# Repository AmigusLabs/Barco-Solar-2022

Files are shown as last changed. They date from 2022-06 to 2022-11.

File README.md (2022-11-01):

# Barco-Solar-2022

Hemos creado de nuevo (<a href="https://www.amiguslabs.org/portfolio_page/barco-solar/" target="_blank">Barco 2018</a> -  <a href="https://www.amiguslabs.org/portfolio_page/amigus-labs-barco-solar19/" target="_blank">Barco 2019</a>) un barco impreso en 3d para participar en la <a href="http://regatasolar.org" target="_blank">Regata Solar de Marine Instruments</a>. Esta vez un trimaran de unos 9Kg de peso y un volumen total de 29 litros.

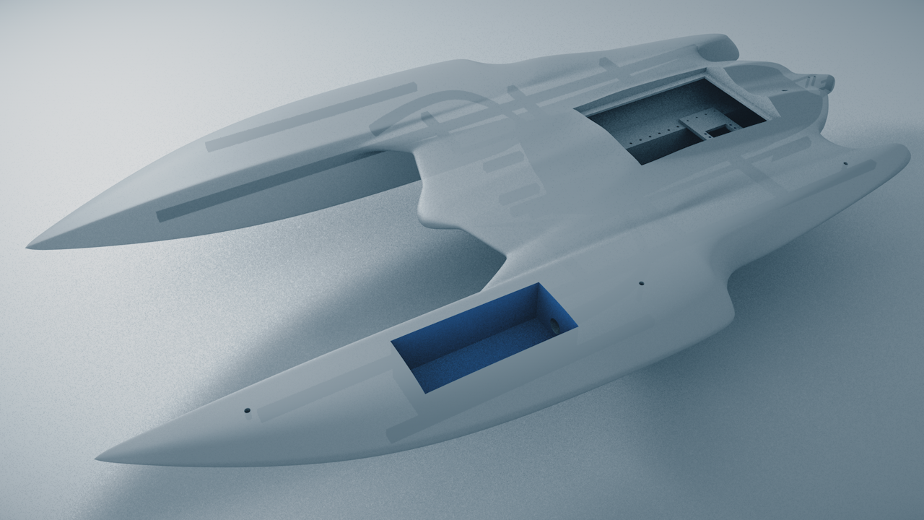
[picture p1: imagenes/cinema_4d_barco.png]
Barco_3D


Se ha diseñado integramente en Cinema 4D, con subdivisión de superficies (curvas Nurbs).

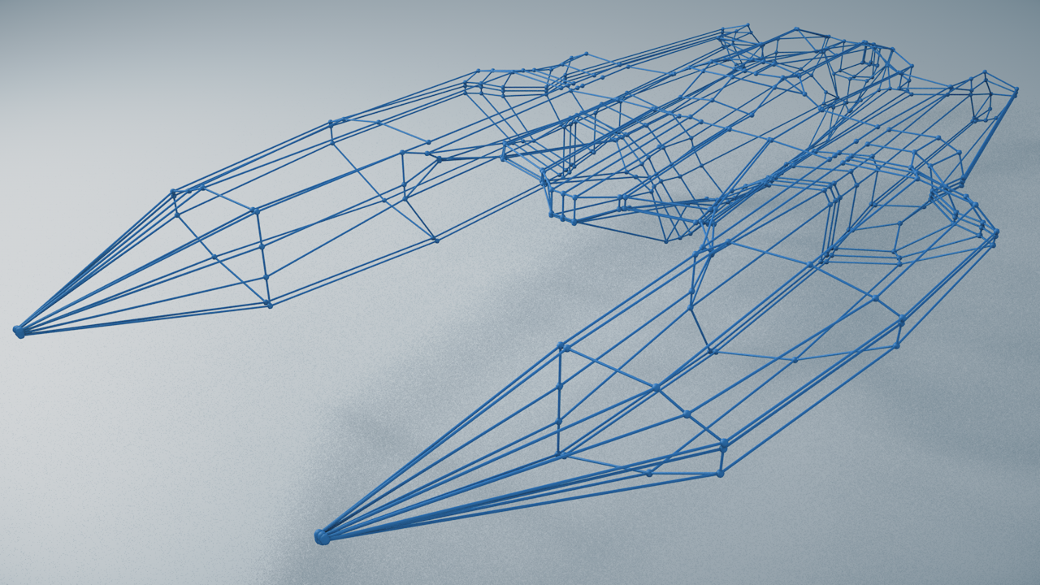
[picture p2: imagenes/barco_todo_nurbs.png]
Nurbs


Una vez modelado, se han dividio en 32 piezas para imprimir, secciones de hasta 250x250x200mm y exportado a STL. Para optimizar la impresión intentamos que cada sección no tardase más de 10 horas en imprimirse, para intentar imprimir por el dia y dormir por la noche :P El software de slicer usado es el Simplify3D y la impresora una Ender 5 Plus.

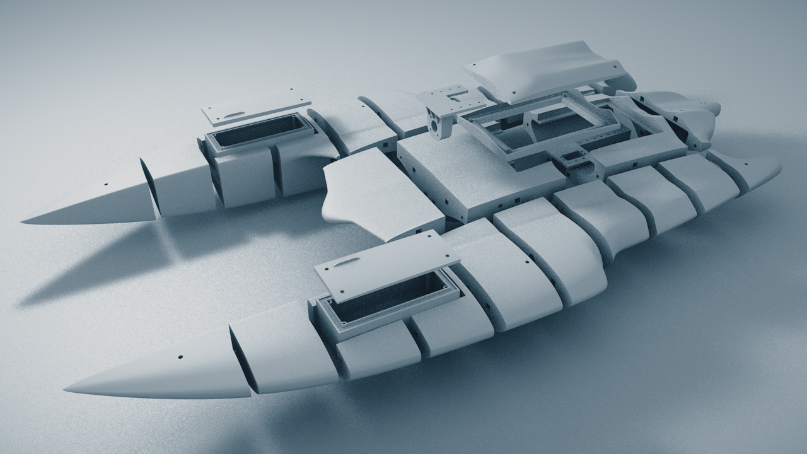
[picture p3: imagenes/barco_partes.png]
Barco_secciones 3D


Evitanto el uso de soportes a la hora de imprimir se han hecho algunas secciones que finalmente se pegan para poder imprimir sobre el lado más plano y evitar luego el postprocesado.

Una vez impresas las piezas, y para facilitar la rigidez a la hora de pegarlas, se han hecho unas secciones en cada pieza para pegar y encajar unos pequeños tubos impresos de unos 10x10x50mm. Se ha pegado todas las partes con pegamento para modelismo comprado en bazar chino, tarda unas 4 horas en secar y quedan las piezas muy rígidas. En las zonas que por sharping de las piezas hizo falta se relleno de masilla para carrocerías de Ceys. 

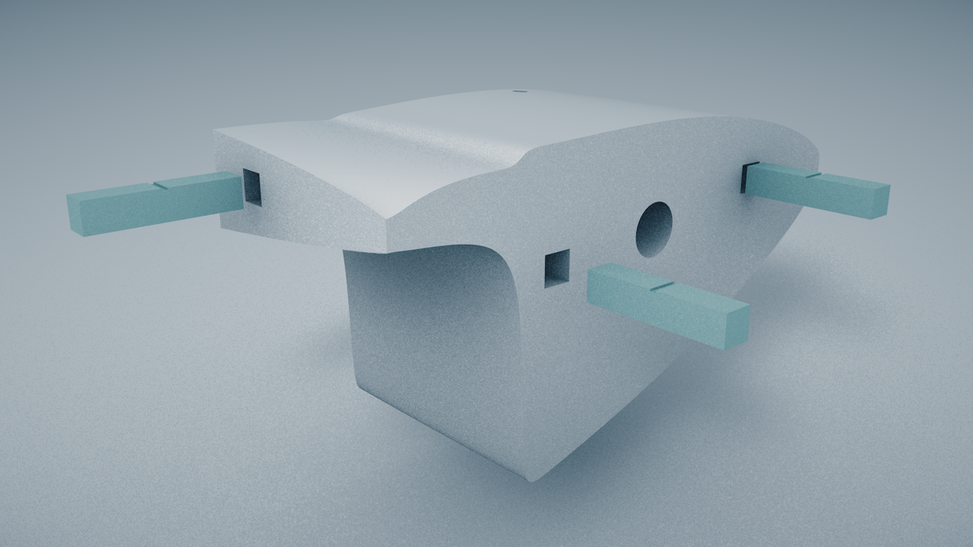
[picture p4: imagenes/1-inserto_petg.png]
Insertos-PETG


Para darle el acabado final, una vez pegadas todas las piezas, se ha aplicado imprimación de color blanco y posteriormente una mano de Epoxi. En el montaje, en las zonas más irregulares se le aplicó un poco de lijado.

Para encajar las partes de electrónica al barco, así como el soporte de la placa solar, se han usado unos insertos de M5 y M3 aplicados con solador, que evitan el uso de tuercas y hacen que las zonas de enrosque queden bien sujetas.

Para las tapas se ha usado goma Eva cortado en laser para hacer las zonas de unión impermeables (gracias a <a href="https://fablableon.org" target="_blank">Fab Lab León</a> y <a href="https://www.esne.es" target="_blank">ESNE</a> por facilitarnos el corte en sus máquinas).

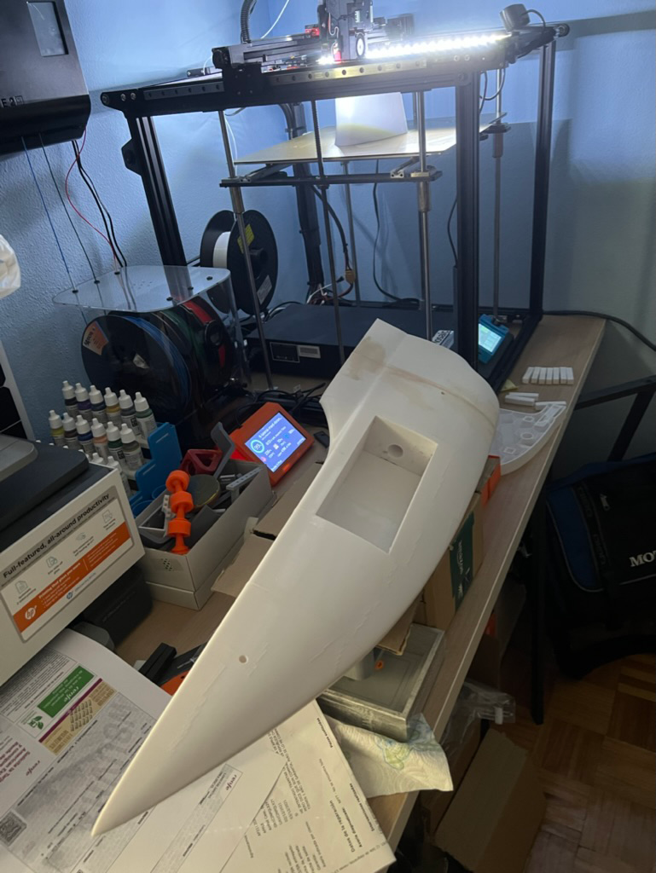
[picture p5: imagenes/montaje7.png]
Montaje


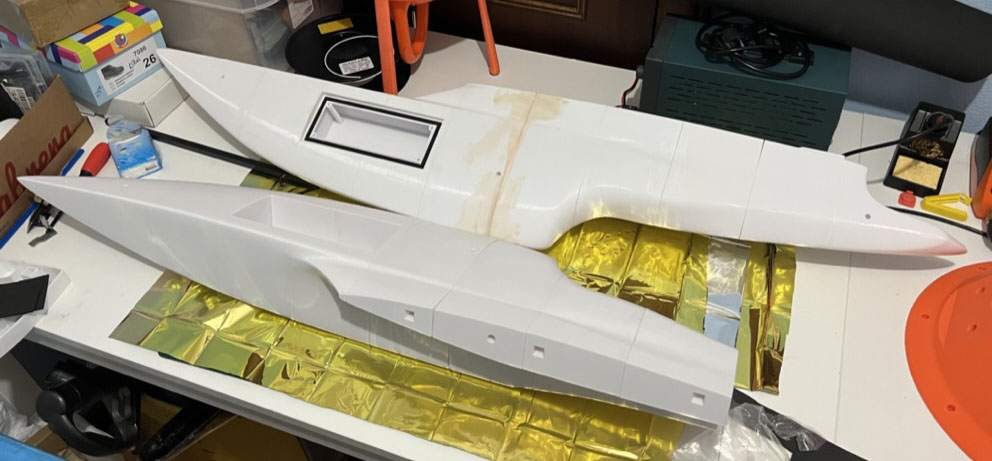
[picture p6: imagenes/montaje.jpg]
Montaje


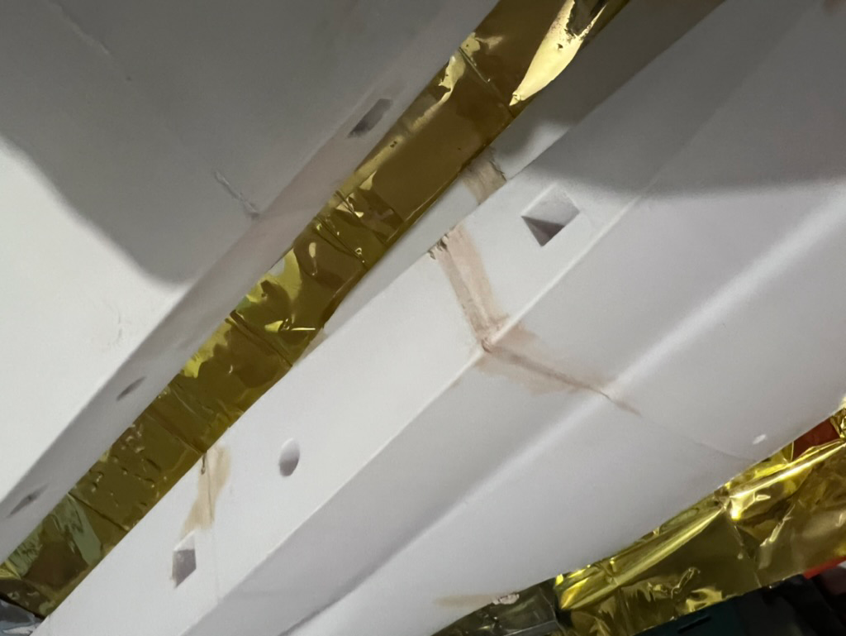
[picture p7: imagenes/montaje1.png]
Montaje


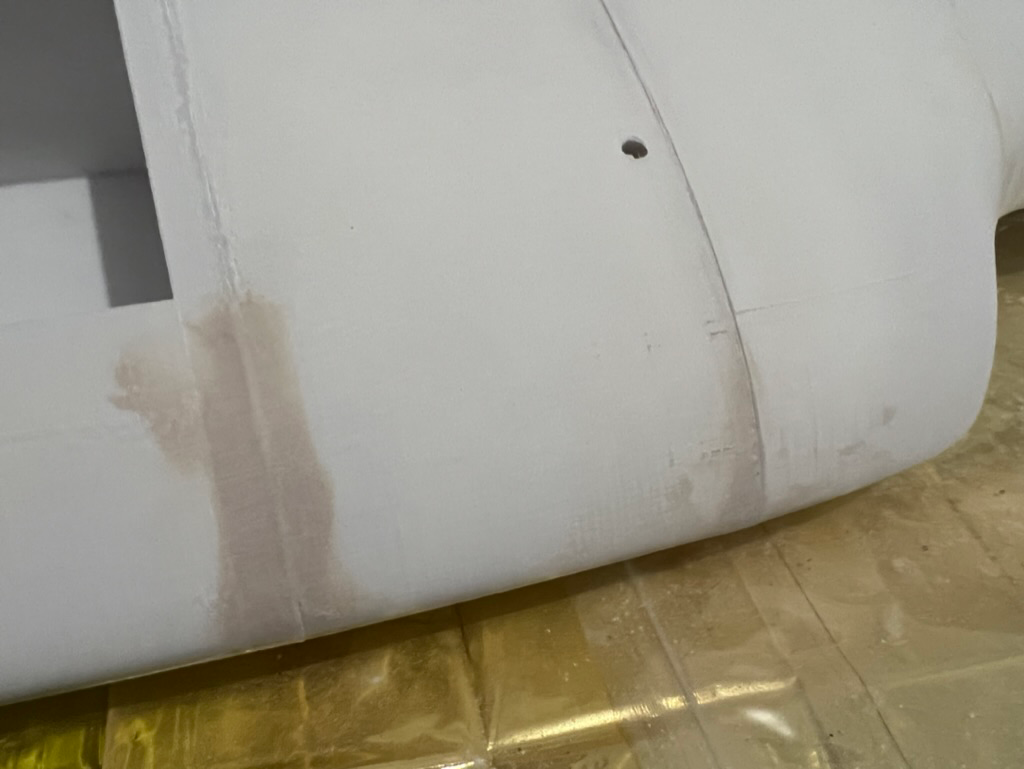
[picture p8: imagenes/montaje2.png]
Montaje


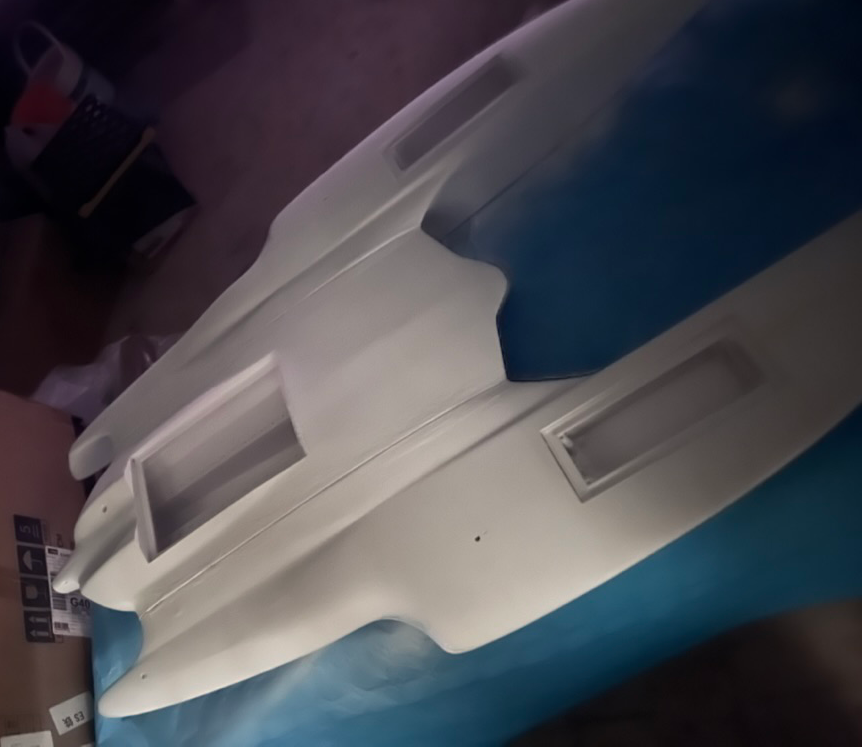
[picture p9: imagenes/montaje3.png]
Montaje


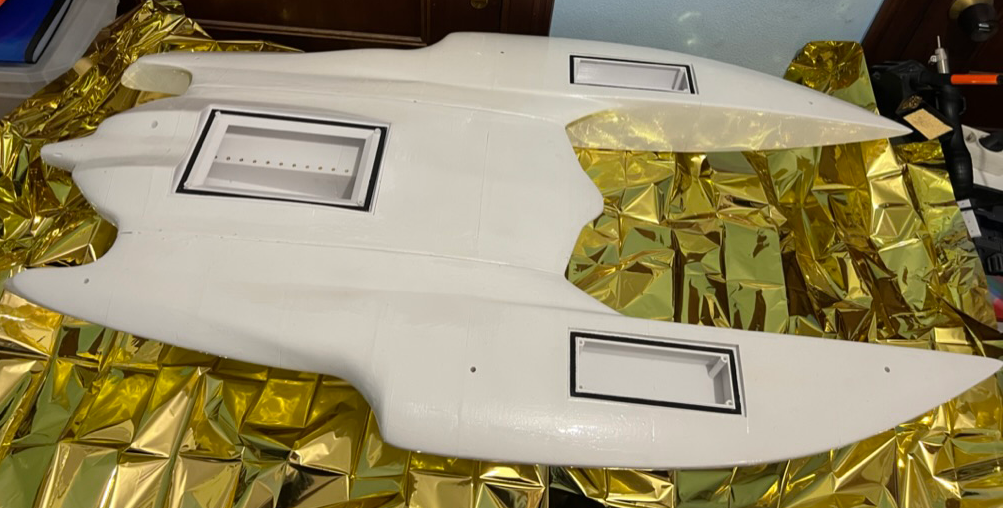
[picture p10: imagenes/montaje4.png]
Montaje


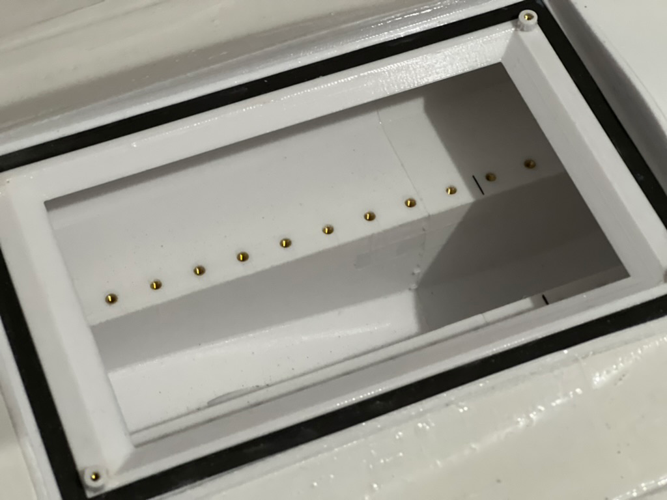
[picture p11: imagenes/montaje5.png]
Montaje


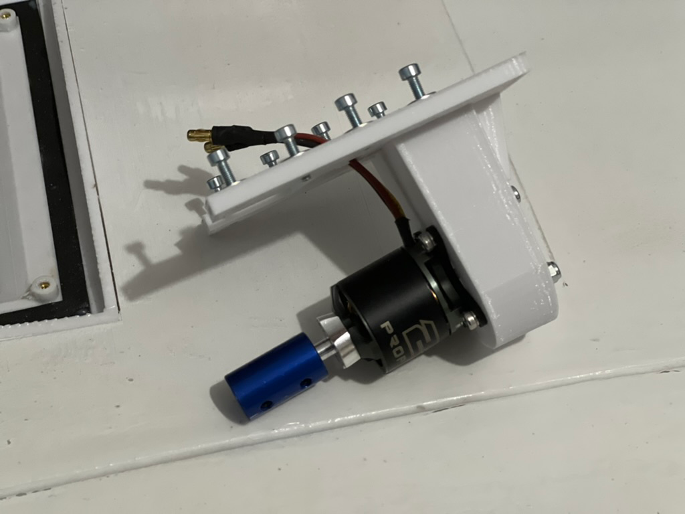
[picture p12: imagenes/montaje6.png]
Montaje


## Electrónica

Hemos intentado hacer una nueva PCB partiendo de un Attiny1614. Se ha diseñado la pcb en KiCAD, integrando un sensor INA219 para la optimización del voltaje y potencia de la placa solar basandonos en la propuesta de <a href="https://github.com/aindustriosa/Solar_MPPT_board" target="_blank">A Industriosa</a> del año 2019.

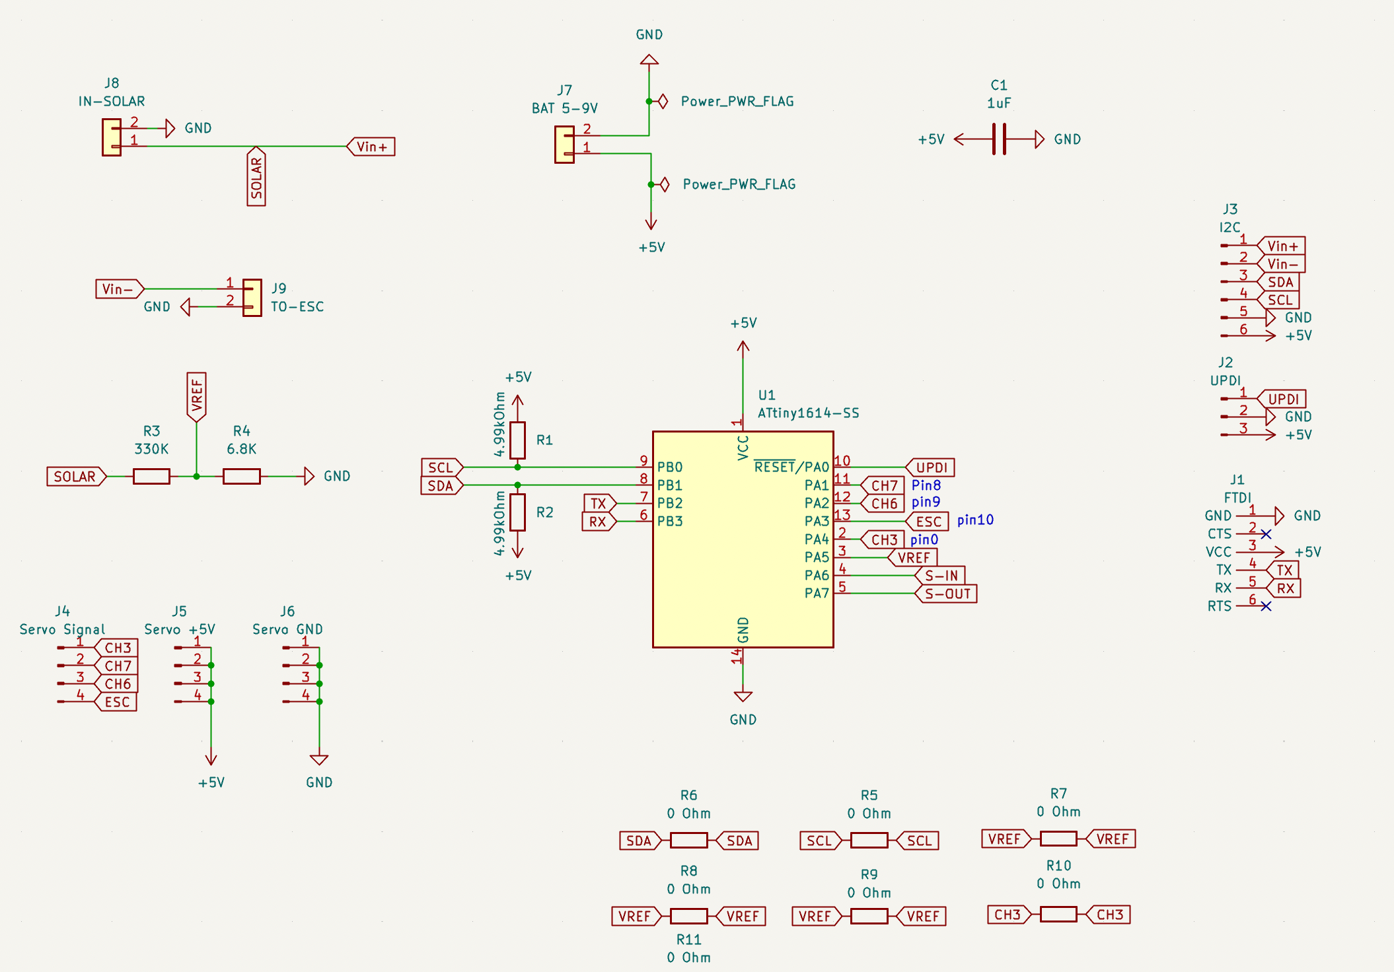
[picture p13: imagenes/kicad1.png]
KiCAD


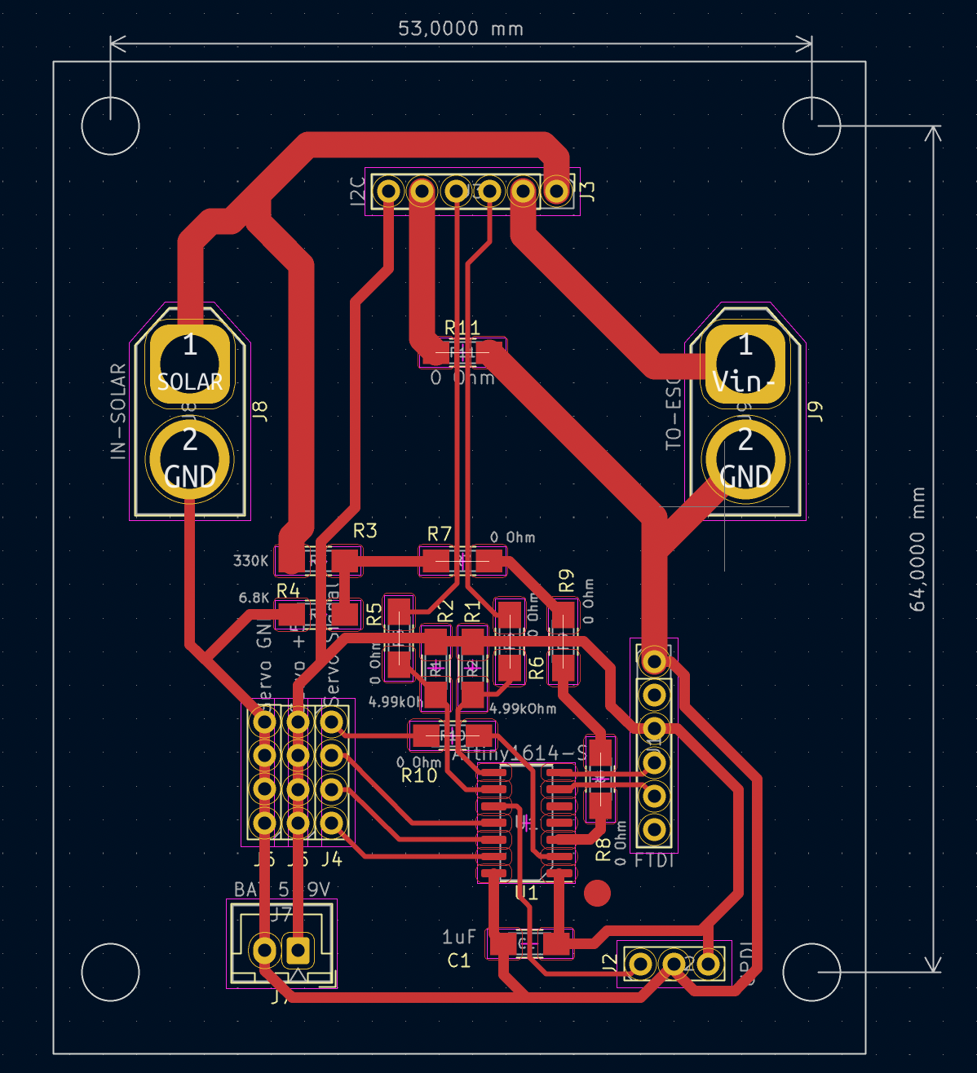
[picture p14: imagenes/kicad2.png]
KiCAD


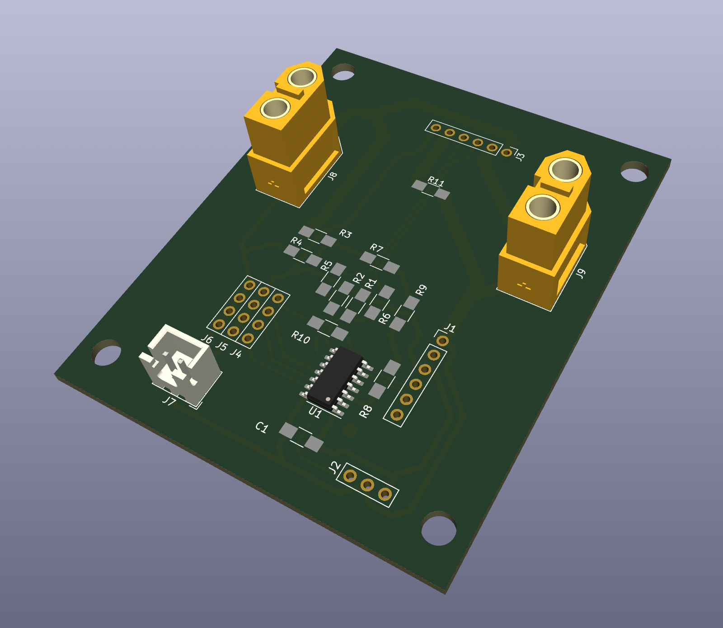
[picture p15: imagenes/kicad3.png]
KiCAD


Con los limites de potencia y memoria del Attiny1614, hemos implementado el uso del sensor así como un divisor de voltaje para leerlo via VREF. Los mensajes enviados desd eel mando RC al receptor, son procesados por el microcontrolador y en caso de exigirle una velocidad mayor al 30% entra en modo automático, y prioriza el rendimiento que este generando la placa solar en ese momento a optener la velocidad optima sin permitir la caida de potencia por un exceso del rendimiento de la placa solar.

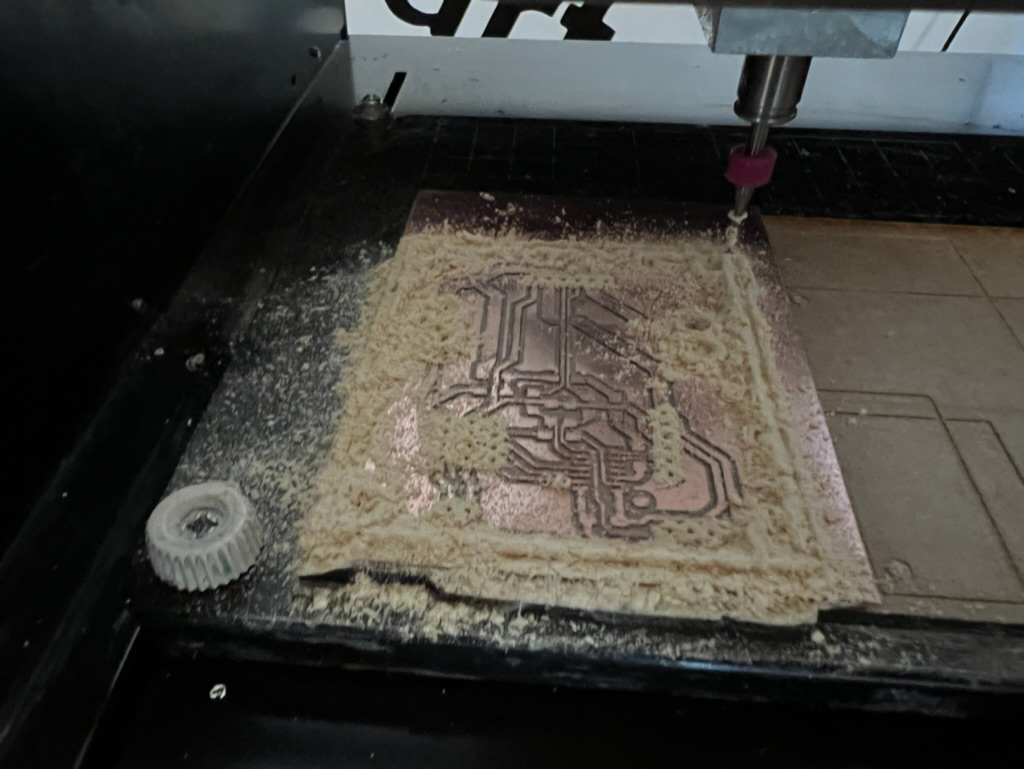
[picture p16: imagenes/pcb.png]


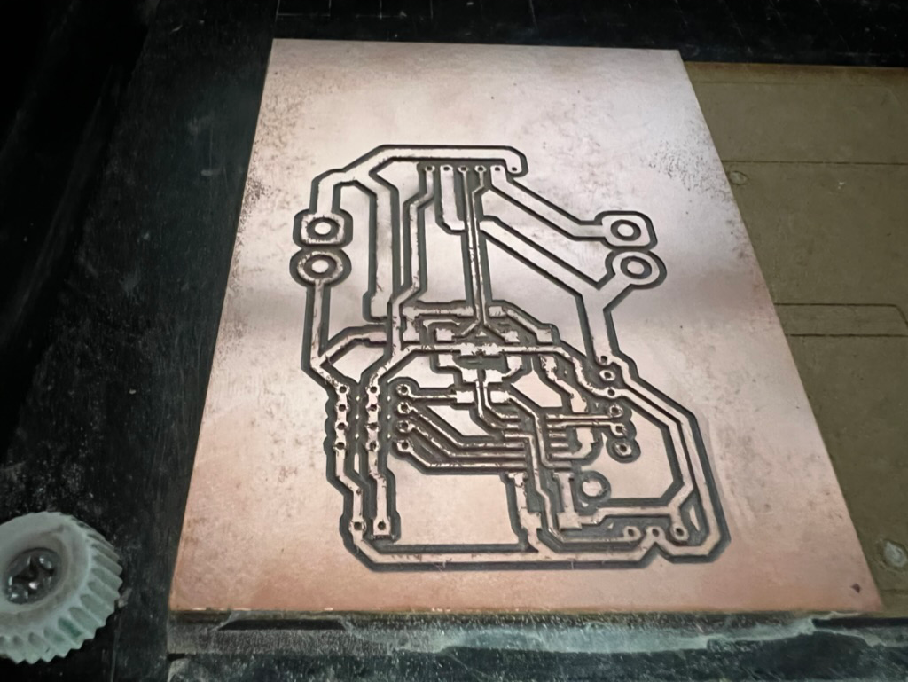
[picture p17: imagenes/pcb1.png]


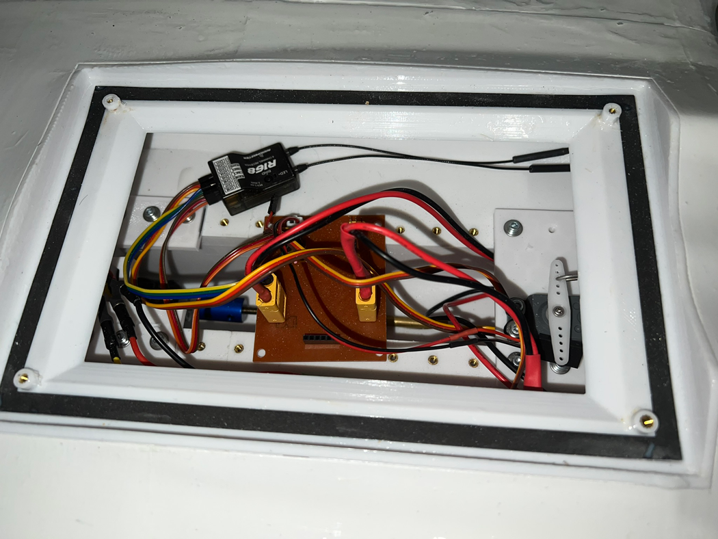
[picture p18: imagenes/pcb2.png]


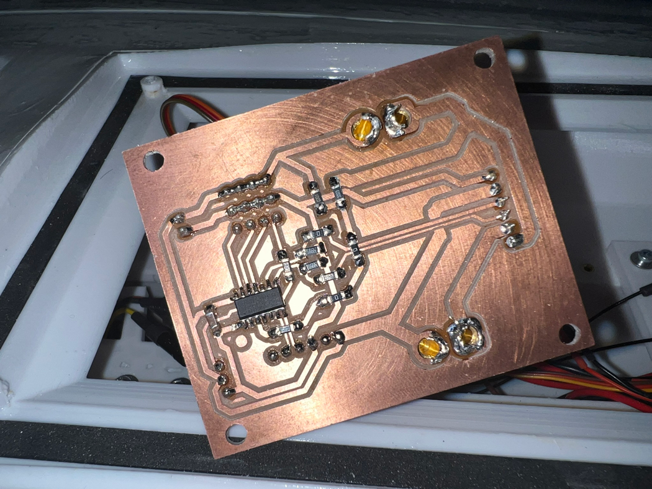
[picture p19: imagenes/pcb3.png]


## Materiales

8x PETG 1Kg Blanco 1.75mm (<a href="https://www.amazon.es/dp/B08C4YP5RS/ref=twister_B08HSFRV2M?_encoding=UTF8&th=1" target="_blank">Amazon</a>)

1x Smartfil FLEX - Filamento Flexible (<a href="https://www.smartmaterials3d.com/flex-filamento#/1-tamano-s_330g/26-diametro-175_mm/29-color-sapphire" target="_blank">Smart Materials 3D</a>)
  
3x Tubos cuadrados de 10x10x500mm - <a href="https://www.clipcarbono.com/es/home/947-tubo-exterior-cuadrado-10x10-mm-interior-cuadrado-8x8-mm-de-fibra-de-carbono-longitud-1000-mm.html" target="_blank">Tubo cuadrado, exterior (10x10 mm.) - interior (8x8 mm.) de fibra de carbono - Longitud 1000 mm.</a> Cortesía de <a href="https://www.clipcarbono.com" target="_blank">ClipCarbono</a>

1x Castropox 4307/1209 Resina Epoxi de usos generales (<a href="https://www.castrocompositesshop.com/es/resinas/1099-resina-epoxi-castropox-43071209.html" target="_blank">Castro Composites</a>)

1x Masilla Carrocerias Ceys (<a href="https://www.amazon.es/Desconocido-M59016-Adhesivo-masilla-carrocerias/dp/B00ITVXML6" target="_blank">Amazon</a>)

3x Imprimación Plástico (<a href="https://www.amazon.es/MTN-IMPRIMACIÓN-PLÁSTICOS-400-ML/dp/B00WG2K6W2/ref=sr_1_15?__mk_es_ES=ÅMÅŽÕÑ&crid=2E2QZXNCDXAI6&keywords=imprimacion&qid=1655512005&sprefix=imprimacion%2Caps%2C124&sr=8-15" target="_blank">Amazon</a>)

1x soporte helice y timón (<a href="https://es.aliexpress.com/item/32901476708.html" target="_blank">Aliexpress</a>)

100x Inserto roscado M3 (<a href="https://www.amazon.es/gp/product/B08BCRZZS3/ref=ppx_yo_dt_b_asin_title_o00_s00?ie=UTF8&th=1" target="_blank">Amazon</a>)

6x Inserto roscado M5 (<a href="https://www.amazon.es/gp/product/B07YSVXWS8/ref=ppx_yo_dt_b_asin_title_o00_s00?ie=UTF8&th=1" target="_blank">Amazon</a>)

1x Acoplamiento Motor 4x5mm (<a href="https://www.amazon.es/gp/product/B09LV3KD4H/ref=ppx_yo_dt_b_asin_title_o05_s00?ie=UTF8&th=1" target="_blank">Amazon</a>)

1x Motor NTM Prop Drive 28-30 800KV (<a href="https://hobbyking.com/es_es/propdrive-v2-2830-800kv-brushless-outrunner-motor.html" target="_blank">Hobbyking</a>)

1x Turnigy Multistart 20A V2 ESC (<a href="https://hobbyking.com/es_es/turnigy-multistar-20a-v2-esc-with-blheli-and-4a-lbec-2-6s.html" target="_blank">Hobbyking</a>)

## Enlaces

- <a href="http://regatasolar.org" target="_blank">Regata Solar de Marine Instruments</a>
- <a href="https://www.amiguslabs.org" target="_blank">Amigus Labs</a>
- <a href="https://www.clipcarbono.com" target="_blank">ClipCarbono</a>
- <a href="http://aindustriosa.org" target="_blank">A Industriosa</a>
- <a href="https://fablableon.org" target="_blank">Fab Lab León</a>
- <a href="https://www.esne.es" target="_blank">ESNE</a>

Proxecto patrocinado por Xunta de Galicia e Amtega Axencia para a Modernización Tecnolóxica

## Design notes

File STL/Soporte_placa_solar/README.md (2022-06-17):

Ficheros para el soporte de la placa solar.

Se ha utilizado 3 tubos cuadrados de fibra de carbono de 10x10x500mm para darle estabilidad a la placa solar, añaden al barco un peso de unos 150gr. Cortesía de <a href="https://www.clipcarbono.com" target="_blank">ClipCarbono</a>

<a href="https://www.clipcarbono.com/es/home/947-tubo-exterior-cuadrado-10x10-mm-interior-cuadrado-8x8-mm-de-fibra-de-carbono-longitud-1000-mm.html" target="_blank">Tubo cuadrado, exterior (10x10 mm.) - interior (8x8 mm.) de fibra de carbono - Longitud 1000 mm.</a>

En los dos insertos centrales del barco va atornillada la placa solar al barco con los soportes, pero los soportes delanteros y traseros la placa solar simplemente va apoyada con velcro.

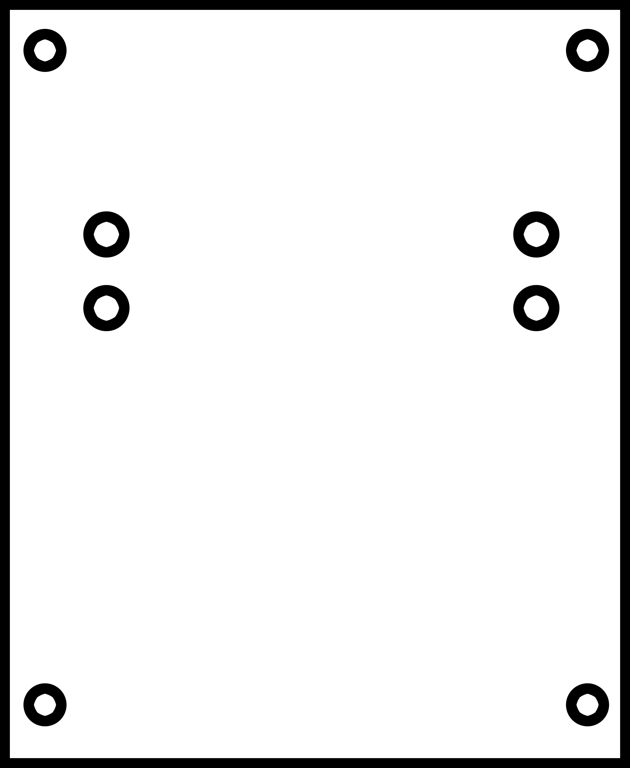
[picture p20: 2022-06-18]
electrónica/Attiny1614_remote/Attiny1614_remote-Corte.png

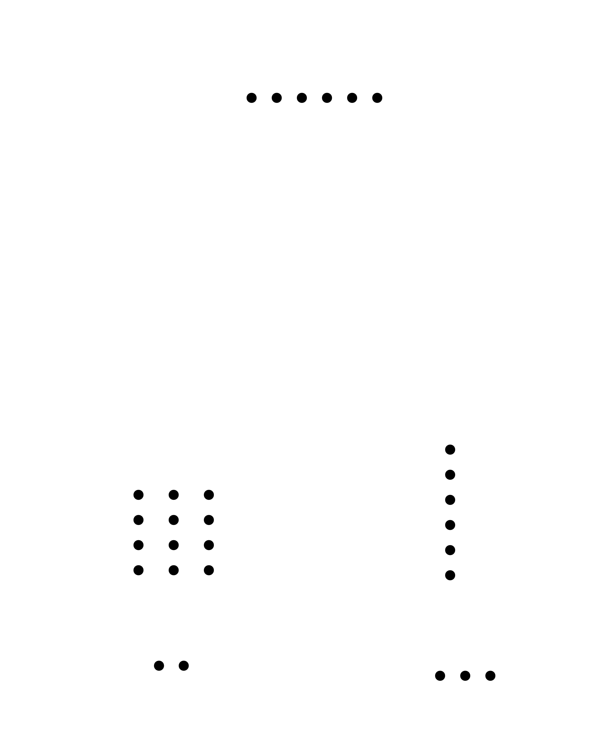
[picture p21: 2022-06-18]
electrónica/Attiny1614_remote/Attiny1614_remote-Agujeros.png

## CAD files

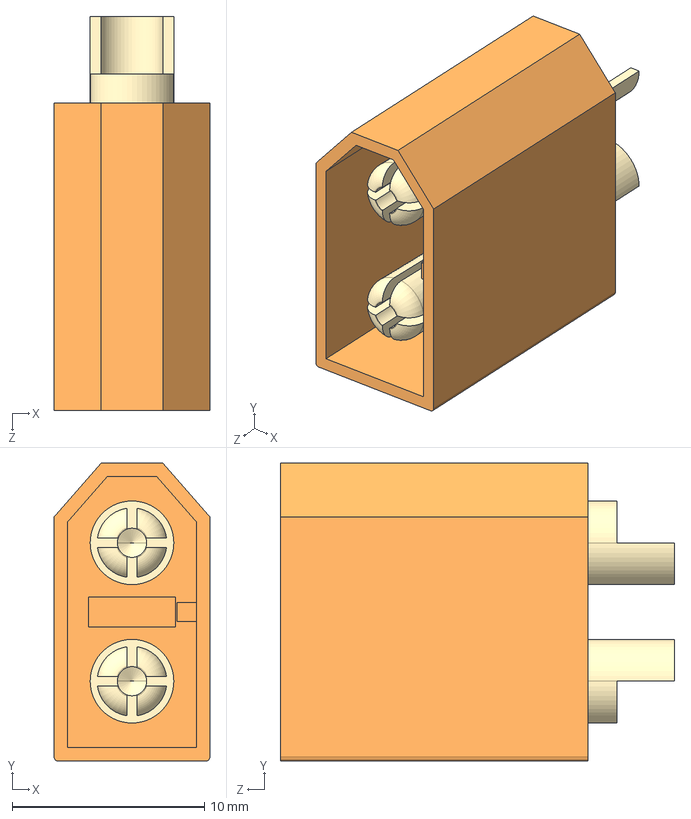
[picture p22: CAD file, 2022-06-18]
electrónica/Attiny1614_remote/librerias/XT60-M/XT60-M.step
8.10 x 15.5 x 20.5 mm

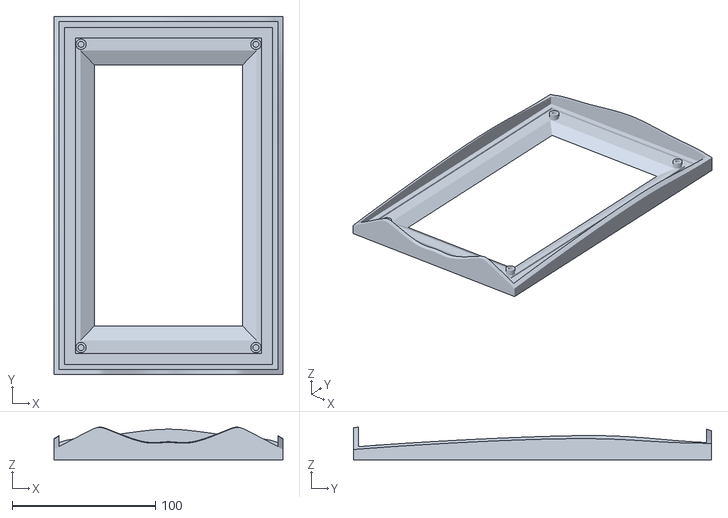
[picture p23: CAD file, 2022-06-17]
STL/Centro_Barco/soporte_tapa_barco.stl
159.7 x 249.7 x 22.9

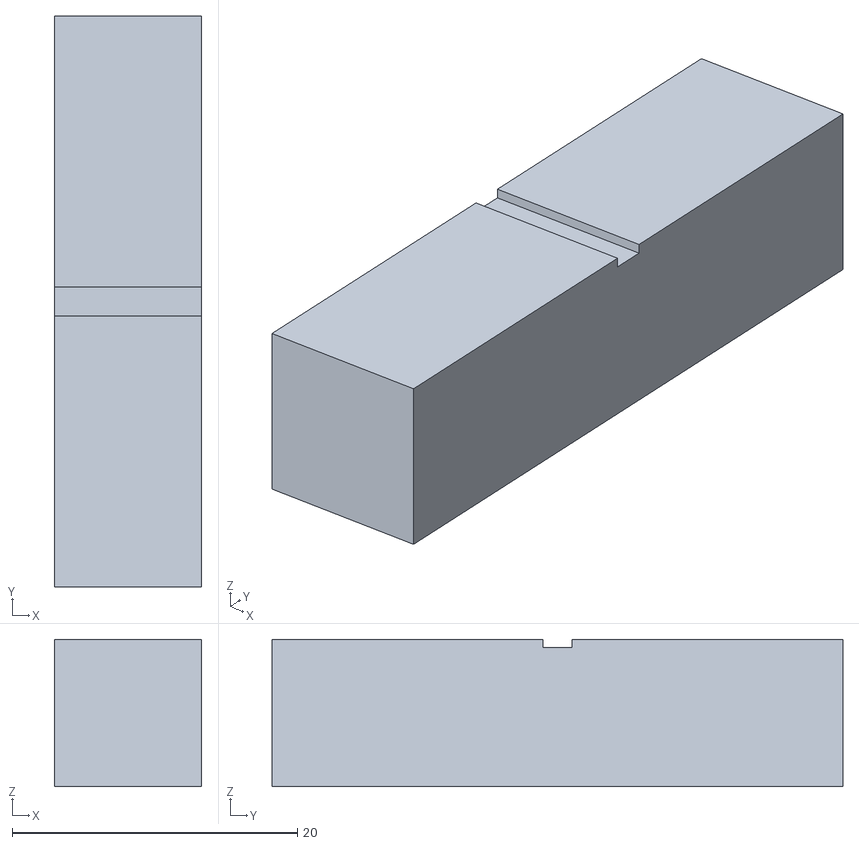
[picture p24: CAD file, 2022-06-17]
STL/Intersecciones_barco/interseccion_corta_10x10x40.stl
10.3 x 40.0 x 10.3

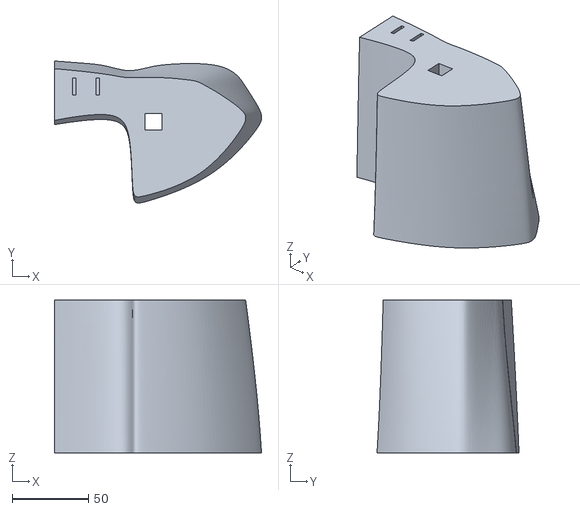
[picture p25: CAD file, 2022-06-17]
STL/Patines_derecha/9-lateral-med-delante_flipX.stl
135.5 x 93.0 x 100.0

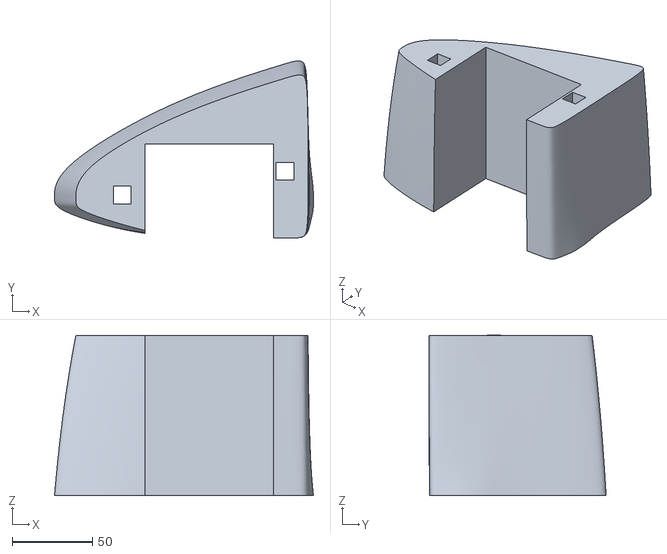
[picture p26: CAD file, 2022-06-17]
STL/Patines_izquierda/4-lateral-med-delante.stl
161.5 x 110.5 x 100.1

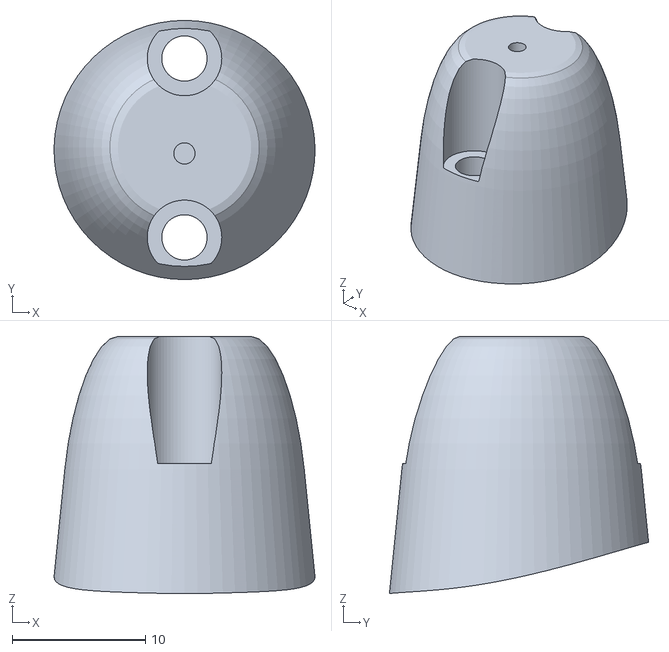
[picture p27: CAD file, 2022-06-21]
STL/soporte_bandera_TPU.stl
19.6 x 19.5 x 19.3

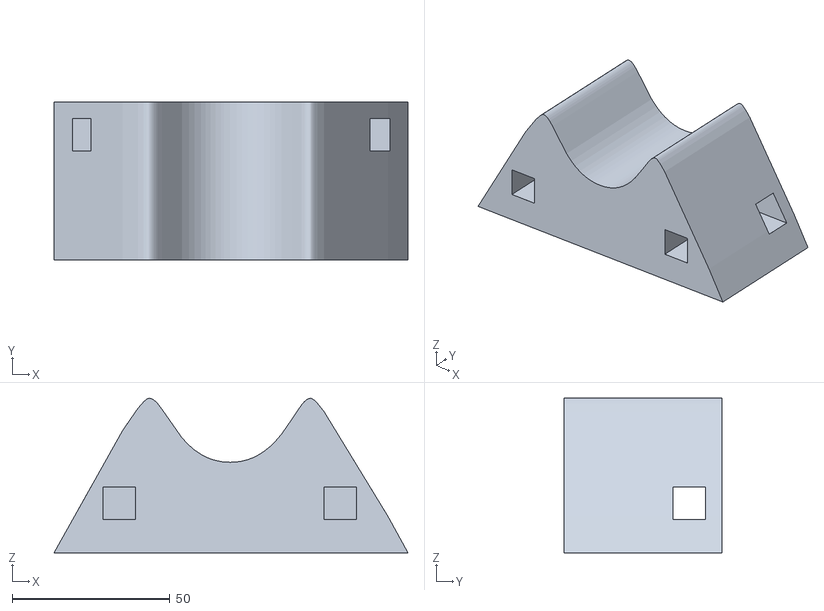
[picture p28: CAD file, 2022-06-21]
STL/Soporte_barco/soportes_barco2.stl
112.4 x 50.0 x 49.0

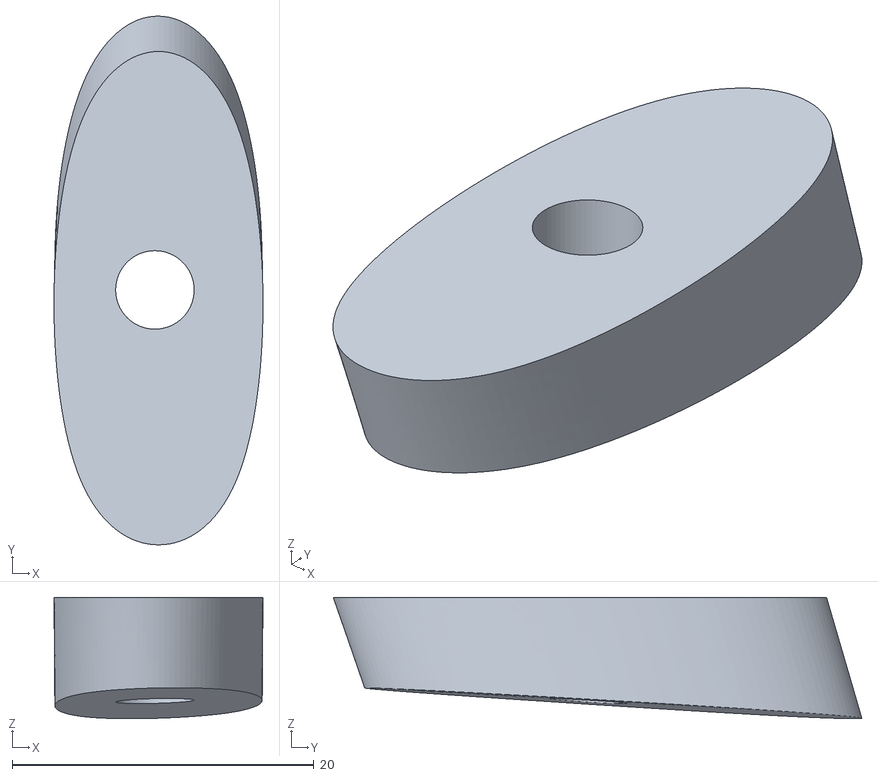
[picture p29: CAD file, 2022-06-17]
STL/Soporte_placa_solar/soporte_delante_TPU_panel.stl
13.8 x 35.0 x 8.04

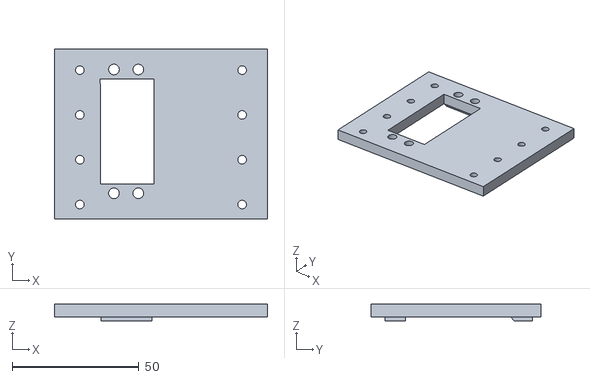
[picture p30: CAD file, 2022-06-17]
STL/Centro_Barco/soporte_servo.stl
84.0 x 67.2 x 6.54

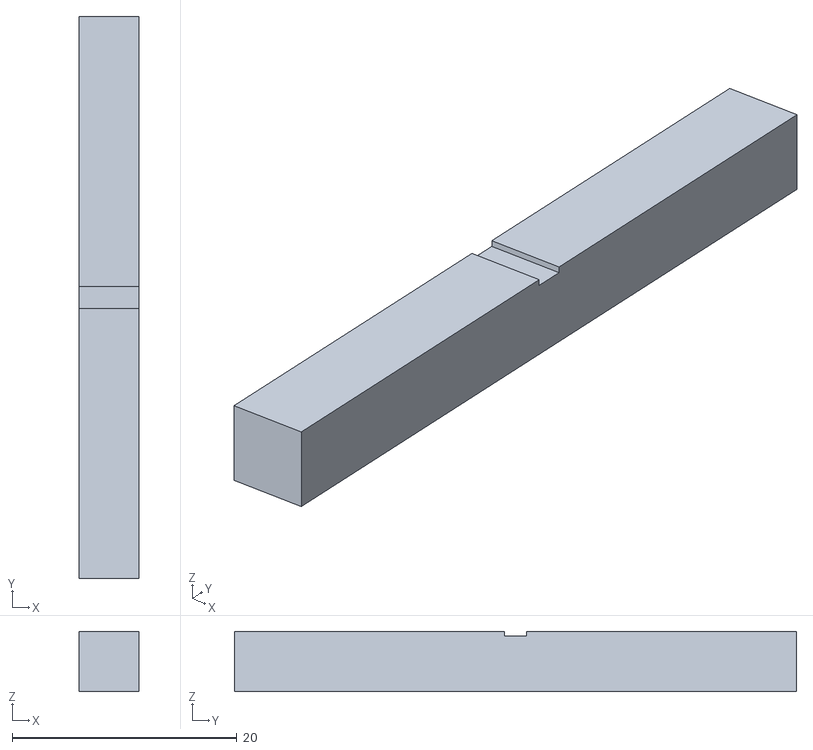
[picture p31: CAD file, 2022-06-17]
STL/Intersecciones_barco/interseccion_6x6x50mm.stl
5.30 x 50.0 x 5.35

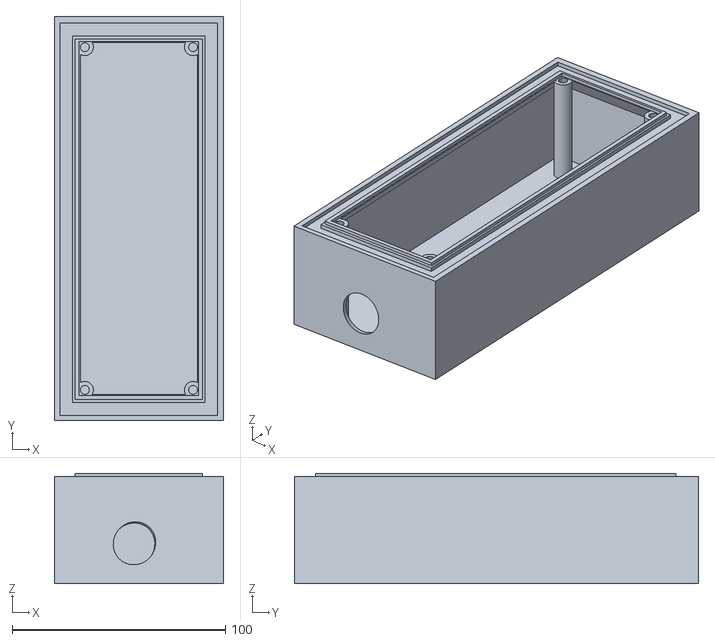
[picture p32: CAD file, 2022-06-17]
STL/Patines_derecha/caja_patin_abajo_flipX.stl
79.5 x 189.5 x 51.7

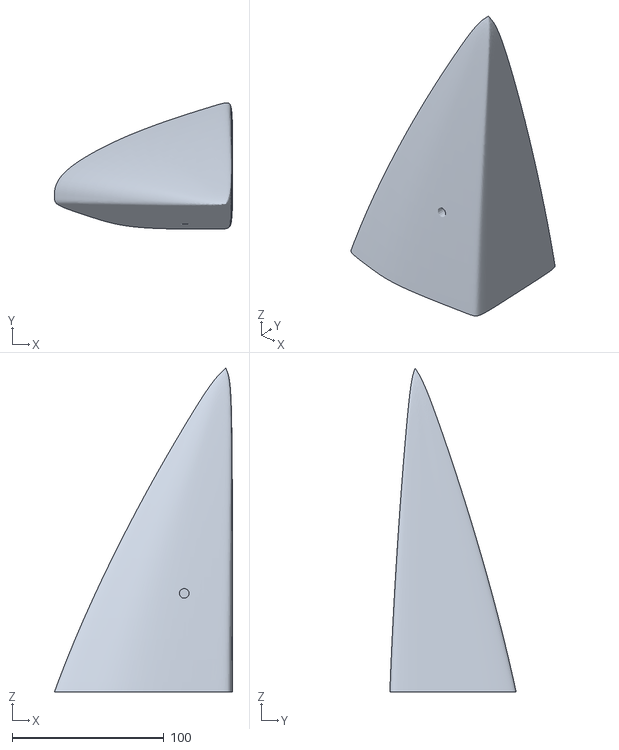
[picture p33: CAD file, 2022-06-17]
STL/Patines_izquierda/1-2-lateral-med-delante.stl
117.4 x 83.2 x 213.5

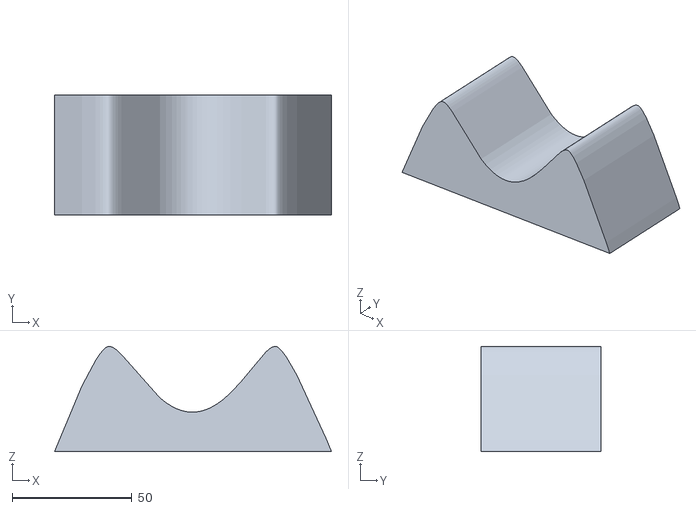
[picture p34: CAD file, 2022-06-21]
STL/Soporte_barco/soportes_barco1.stl
115.7 x 50.0 x 43.9

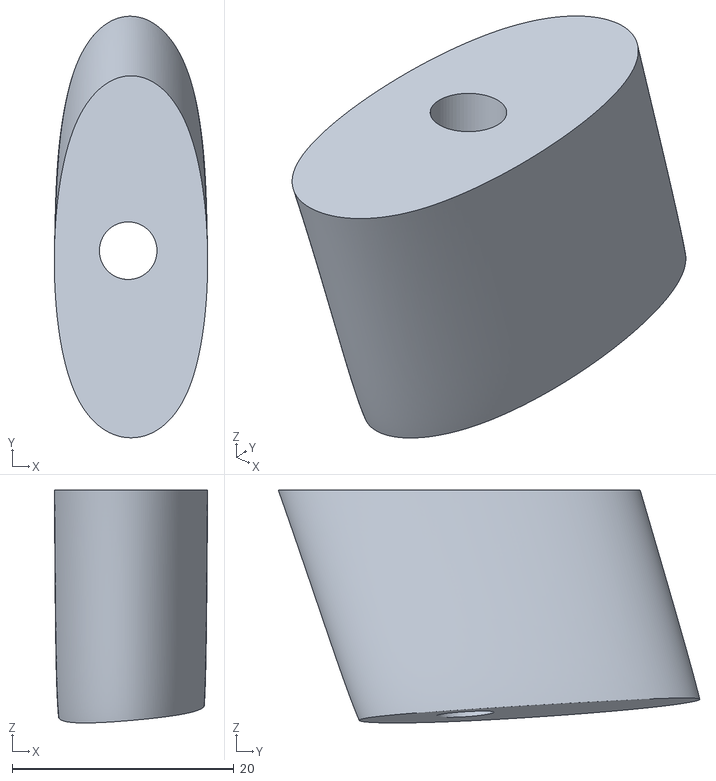
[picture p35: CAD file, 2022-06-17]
STL/Soporte_placa_solar/soporte_detras_TPU_panel.stl
13.8 x 38.1 x 21.0

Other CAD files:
STL/Centro_Barco/soporte_motor.stl
STL/Intersecciones_barco/interseccion10x10x50.stl
STL/Patines_derecha/7-lateral-med-delante_flipX.stl
STL/Patines_izquierda/3-lateral-med-delante.stl
STL/Patines_derecha/1-2-lateral-med-delante_flipX.stl
STL/Patines_derecha/10-lateral-med-delante_flipX.stl
STL/Patines_derecha/11-lateral-med-delante_flipX.stl
STL/Patines_derecha/3-lateral-med-delante_flipX.stl
STL/Patines_derecha/4-lateral-med-delante_flipX.stl
STL/Patines_derecha/5-lateral-med-delante_flipX.stl
STL/Patines_derecha/6-lateral-med-delante_flipX.stl
STL/Patines_derecha/8-lateral-med-delante_flipX.stl
STL/Patines_derecha/caja_patin_arriba_flipX.stl
STL/Patines_izquierda/10-lateral-med-delante.stl
STL/Patines_izquierda/11-lateral-med-delante.stl
STL/Patines_izquierda/5-lateral-med-delante.stl
STL/Patines_izquierda/6-lateral-med-delante.stl
STL/Patines_izquierda/7-lateral-med-delante.stl
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

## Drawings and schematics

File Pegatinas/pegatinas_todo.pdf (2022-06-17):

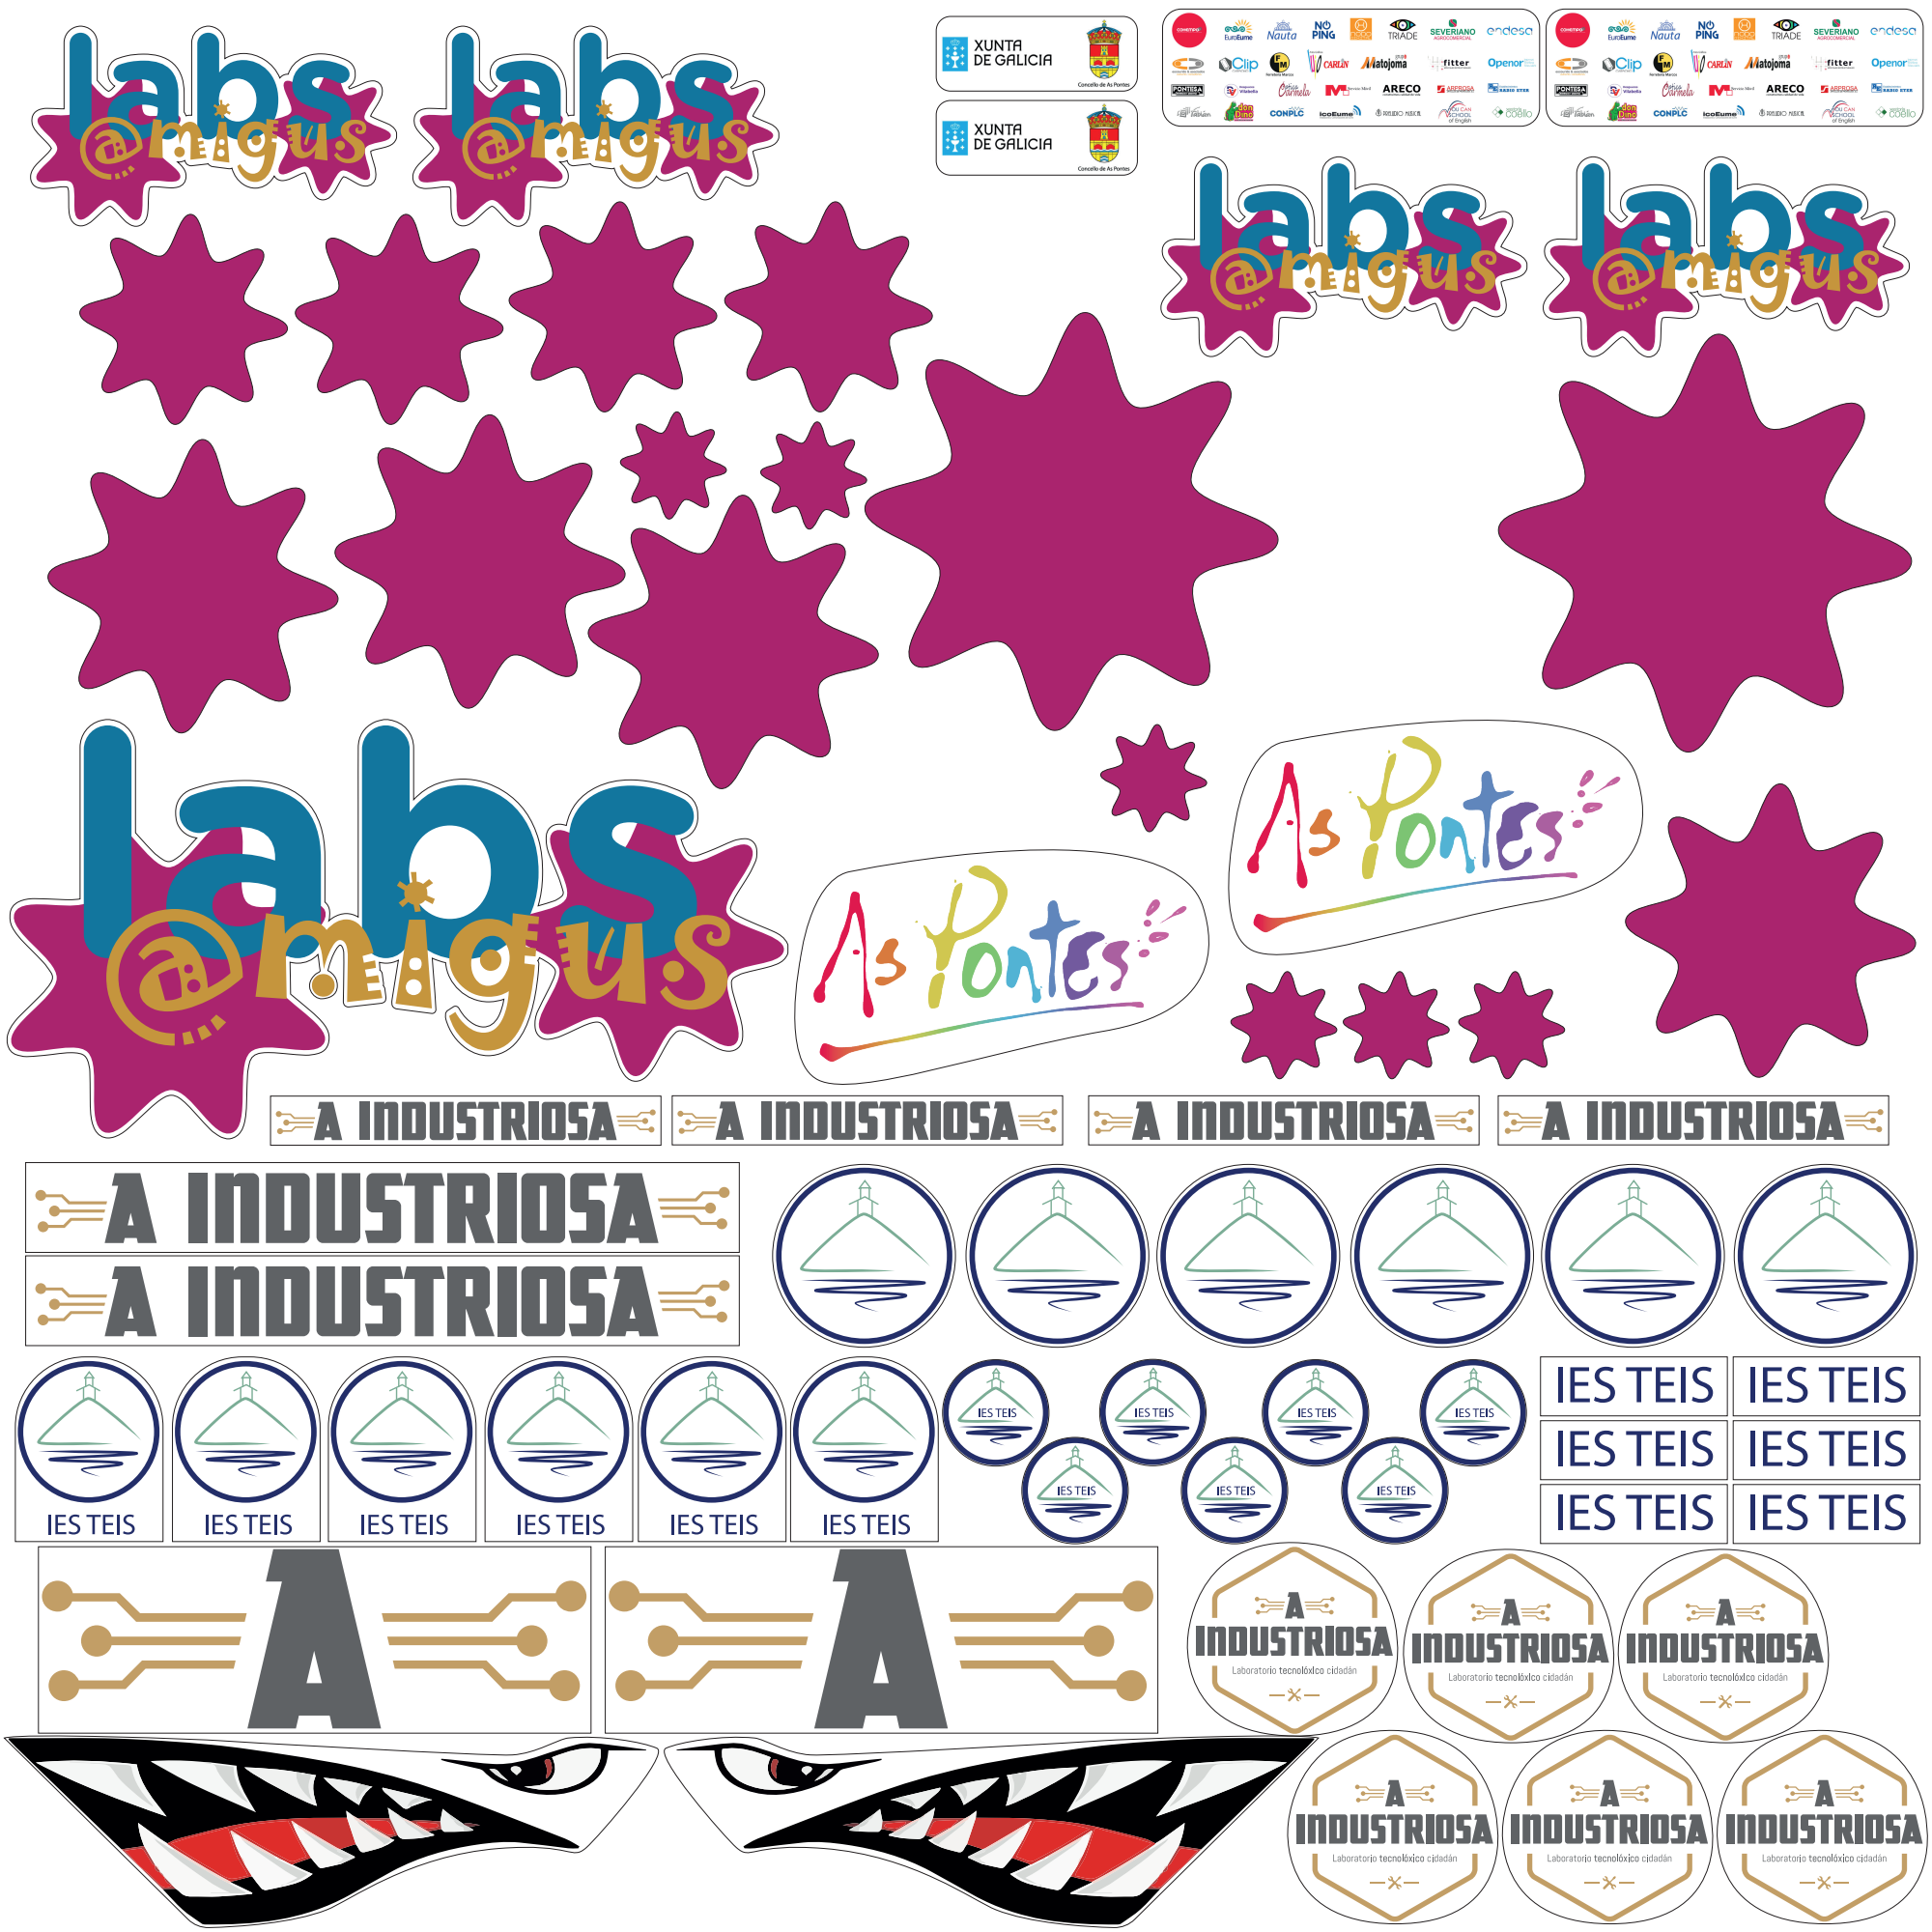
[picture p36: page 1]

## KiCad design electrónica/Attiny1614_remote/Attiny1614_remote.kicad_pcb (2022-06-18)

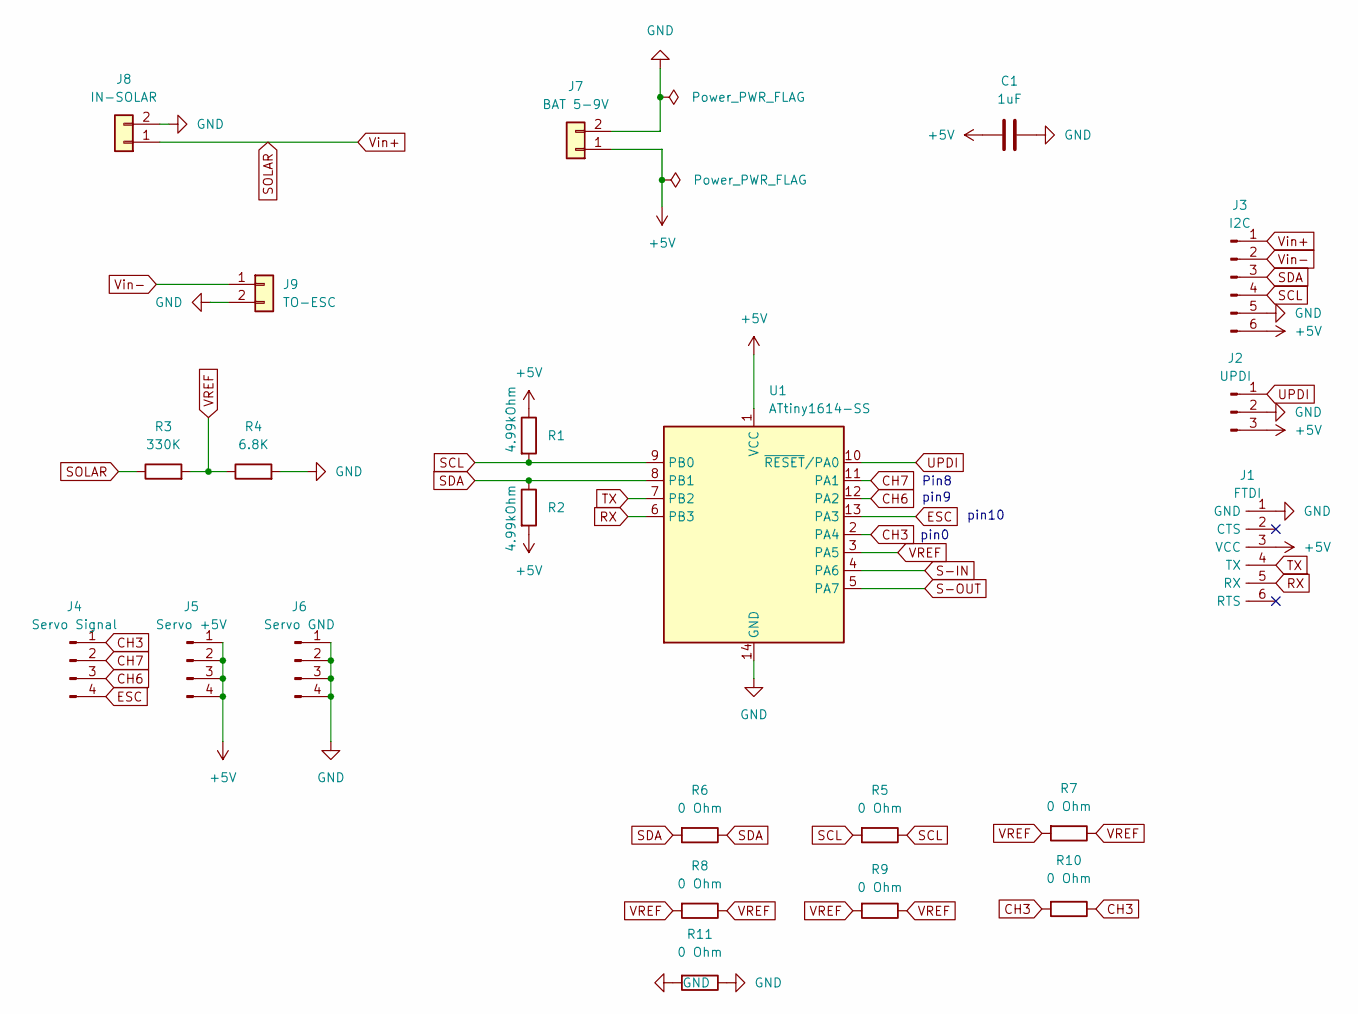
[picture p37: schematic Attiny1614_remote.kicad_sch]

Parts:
C1: 1uF; C_1206
J1: FTDI; PinHeader_1x06_P2.54mm_Vertical_THT_D1mm
J2: UPDI; PinHeader_1x03_P2.54mm_Vertical_THT_D1mm
J3: I2C; PinHeader_1x06_P2.54mm_Vertical_THT_D1mm
J4: Servo Signal; PinHeader_1x04_P2.54mm_Vertical_THT_D1mm
J5: Servo +5V; PinHeader_1x04_P2.54mm_Vertical_THT_D1mm
J6: Servo GND; PinHeader_1x04_P2.54mm_Vertical_THT_D1mm
J7: BAT 5-9V; JST_XH_B2B-XH-A_1x02_P2.50mm_Vertical
J8: IN-SOLAR; AMASS_XT60-F_1x02_P7.20mm_Vertical
J9: TO-ESC; AMASS_XT60-F_1x02_P7.20mm_Vertical
R1, R2: 4.99kOhm; R_1206
R3: 330K; R_1206
R4: 6.8K; R_1206
R5, R6, R7, R8, R9, R10, R11: 0 Ohm; R_1206
U1: ATtiny1614-SS; SOIC-14_3.9x8.7mm_P1.27mm

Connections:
+5V: C1.1, J1.3 (VCC), J2.3, J3.6, J5.1, J5.2, J5.3, J5.4, J7.1, R1.1, R2.2, U1.1 (VCC)
CH3: J4.1, R10.1, R10.2, U1.2 (PA4)
CH6: J4.3, U1.12 (PA2)
CH7: J4.2, U1.11 (PA1)
ESC: J4.4, U1.13 (PA3)
GND: C1.2, J1.1 (GND), J2.2, J3.5, J6.1, J6.2, J6.3, J6.4, J7.2, J8.2, J9.2, R4.2, R11.1, R11.2, U1.14 (GND)
RX: J1.5 (RX), U1.6 (PB3)
S-IN: U1.4 (PA6)
S-OUT: U1.5 (PA7)
SCL: J3.4, R1.2, R5.1, R5.2, U1.9 (PB0)
SDA: J3.3, R2.1, R6.1, R6.2, U1.8 (PB1)
SOLAR: J3.1, J8.1, R3.1
TX: J1.4 (TX), U1.7 (PB2)
UPDI: J2.1, U1.10 (~RESET/PA0)
VREF: R3.2, R4.1, R7.1, R7.2, R8.1, R8.2, R9.1, R9.2, U1.3 (PA5)
Vin-: J3.2, J9.1

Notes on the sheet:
Pin8
pin10
pin0
pin9

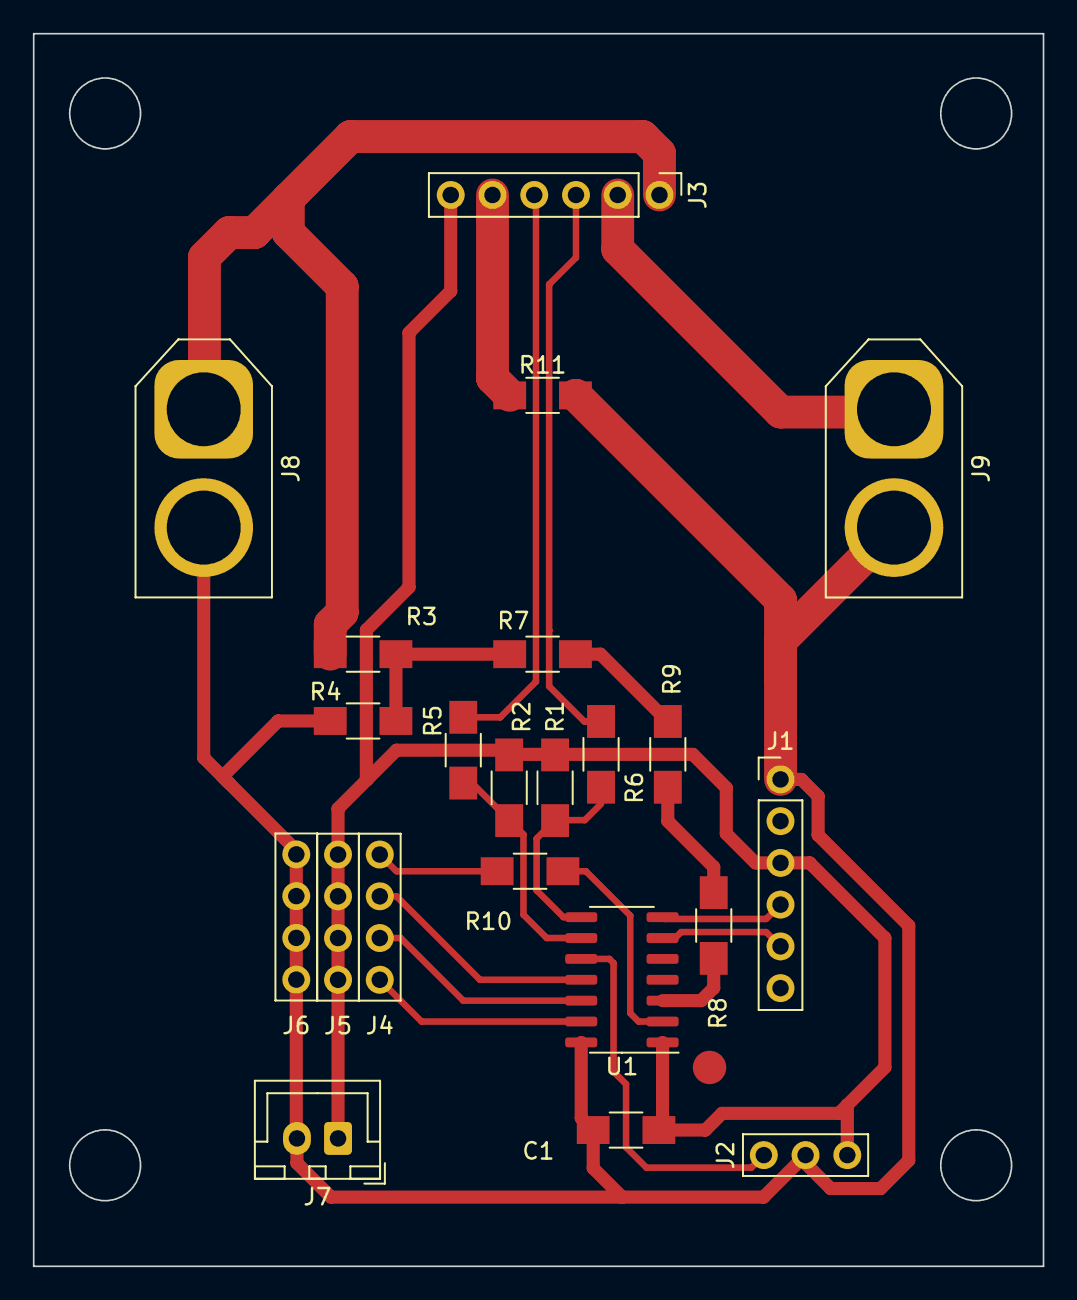
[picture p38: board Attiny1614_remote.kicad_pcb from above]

Board: 2 copper layers, 61.4 x 75.0 mm, 22 parts (0 on the bottom side), 14 nets.

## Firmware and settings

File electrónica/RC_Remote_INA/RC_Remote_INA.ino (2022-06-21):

#include <Streaming.h> //para la salida de print y endl http://arduiniana.org/libraries/streaming/
#include "current.h"
#include "Config.h"
#include <Servo.h>
#include "Arduino.h"
#include "ListLib.h"

//---------------DEBUG---------------
//#define PIN_DEBUG 8
bool DEBUG = true;
//-------------------P&O SETTINGS--------------


#define PO_ENABLE_SPEED 30
#define PO_TIMER 150
#define PO_STEP 1
#define po_samples 20

List<float> listVol;
List<float> listAmp;

float v = 0;
float i = 0;
float p = 0;
float Av = 0; //Delta Volts
float Ap = 0; //Delta Power
float p_prev = 0;
float v_prev = 0;
float ms = 0;
float velo = 0;

float i_media = 0;
float v_media = 0;
int cnt_po = 1;
int cnt_po_ina_samples = 0;
int po_speed = 0; //valor d po_speed cuando entramos en po
bool po_enable = false;
void PO_timer_callback();

//-----------------ENTRADAS----------------------
#define RECEPTOR_CH3_PIN 0 // Channel 3 velocity
#define RECEPTOR_CH6_PIN 9 // Channel 6 control Auto/Manual
#define RECEPTOR_CH7_PIN 8 // Channel 7

#define SALIDA_ESC_PIN 10 // to servo or ESC
#define initpulse   1000 //algunos ESC se inician con un pulso de 1000 otros cn 1500 otros cn 2000
//#define inc_steps   1

Servo ESC;

int vel = initpulse;

//-----------------ESC----------------------
#define sensibilidad 3
int velocidad = 0;

//-----------------INA219---------------
#define Ki 270
#define Kv

//--------------SWITCH--------------
int dato_switch = 0;
unsigned long timeout_pwm_micros = 50000;

void setup() {
  Serial.begin(115200);
  pinMode(RECEPTOR_CH3_PIN, INPUT);
  pinMode(RECEPTOR_CH6_PIN, INPUT);
  pinMode(RECEPTOR_CH7_PIN, INPUT);
  ESC.attach(SALIDA_ESC_PIN);
  delay(10);
  delay(1000);

  init_INA219(0);

  po_enable = false; //indicamos que iniciamos en speed

  for (int i = 0; i <= po_samples; i++)
  {
    listVol.Add(0);
    listAmp.Add(0);
  }

}

bool switchActivado()
{
  unsigned long value1 = pulseIn(RECEPTOR_CH6_PIN, HIGH, timeout_pwm_micros);
  unsigned long value2 = pulseIn(RECEPTOR_CH6_PIN, HIGH, timeout_pwm_micros);
  if ((value1 > 1200) && (value2 > 1200))
  {
    Serial.println("Modo Manual");
    return false;
  }
  Serial.println("Modo Automático");
  return true;
}


void loop() {
  velo = pulseIn(RECEPTOR_CH3_PIN, HIGH);
  velocidad = map(velo, 1000, 2000, 0, 100);
  //speed = speed/sensibilidad;

  Serial.print("Velocidad: ");
  Serial.println(velocidad);
  Serial.print("Voltaje: ");
  Serial.print(get_LoadVolts());
  Serial.print(" - Potencia: ");
  Serial.println(get_LoadCurrent());

  if (velocidad >= 100) {
    velocidad = 100;
  }


  listVol.RemoveFirst();
  listAmp.RemoveFirst();

  listVol.Add(get_LoadVolts());
  listAmp.Add(get_LoadCurrent() / Ki);


  if (switchActivado())
  {

    if (velocidad < 0) velocidad = 0;
    if (velocidad < PO_ENABLE_SPEED) { //Si po_speed <30, vel fijada x mando
      po_enable = false; //indicamos que estamos en modo speed
      cnt_po = 1; //reseteamos indicador de P&O para que cuando comience se resetee en ciclo 1 y pille speed
    } else {

      if (cnt_po == 1) {
        for (int i = 0; i <= po_samples; i++)
        {
          listVol.Add(get_LoadVolts());
          listAmp.Add(get_LoadCurrent() / Ki);
        }
        cnt_po == 0;

        po_enable = true;
        po_speed = PO_ENABLE_SPEED;
        po_speed += PO_STEP;

      }
    }



    v_media = 0;
    i_media = 0;

    for (int i = 0; i < po_samples; i++)
    {
      v_media += listVol[i];
      i_media += listVol[i];
    }

    v = v_media / po_samples;
    i = i_media / po_samples;

    p = i * v;

    Av = v - v_prev;
    Ap = p - p_prev;

    //DEBUG = digitalRead(PIN_DEBUG);
    //Si po_speed >50 entra P&0
    /*
      ----------COMIENZA P&O--------------------
    */

    if (Ap == 0) {
      po_speed += PO_STEP;
      //Serial.println("AP=0");
    } else {
      if (Ap > 0) {
        //Serial.println("AP>0");
        if (Av < 0) {
          po_speed += PO_STEP;
          velocidad = po_speed;
          //Serial.println("B2");

        } else if (Av >= 0) {
          po_speed -= PO_STEP;
          velocidad = po_speed;
          //Serial.println("B1");
        }
      } else {
        //Serial.println("AP<0");
        if (Av > 0) {
          po_speed += PO_STEP;
          velocidad = po_speed;
          //Serial.println("A2");
        } else if (Av <= 0) {
          po_speed -= PO_STEP;
          velocidad = po_speed;
          //Serial.println("A1");
        }
      }
    }

  }

  p_prev = p;
  v_prev = v;


  if (po_speed >= 100) {
    po_speed = 100;
  }

  if (DEBUG) {
    Serial.println("TX_PPM,Mode,ESC_PPM,Voltage,Current,Power");
    Serial.println();
    Serial.print(velocidad);
    Serial.print(",");
    if (po_enable) {
      Serial.print("---Activo---,Vel: "); //modo P
      Serial.print(po_speed);
    } else {
      Serial.print("---Desactivado---,Vel: "); // modo s
      Serial.print(velocidad);
    }
    Serial.print(",Vol: ");
    Serial.print(v);
    Serial.print(",Pow: ");
    Serial.print(i);
    Serial.println(",");

  }



  // Serial.print("Velocidad procesada: ");
  // Serial.println(velocidad);

  ms = map(velocidad, 0, 100, 1000, 2000);
  ESC.writeMicroseconds(ms);
  delay(15);

}

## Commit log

2022-06-17 ficheros Centro Barco
    Limite 25Mb, se han comprimido algunos ficheros como .zip
    [soporte_tapa_barco.stl]
2022-06-18 Kicad images
2022-06-21 update STL
    Nuevas piezas soporte bandera TPU y soporte barco
    [soporte_bandera_TPU.stl, soportes_barco1.stl, soportes_barco2.stl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]
